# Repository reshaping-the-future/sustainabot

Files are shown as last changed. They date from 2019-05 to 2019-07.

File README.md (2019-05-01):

# Sustainabot
Sustainabot is a mini robot printer that uses everyday materials to create shapes and patterns.

The robot's body designs, circuit layouts, microcontroller code and accompanying Android app source code are all released under the Apache 2.0 license.

See the [toolkit website](http://digitalinclusiontoolkit.org/) and [research project website](http://www.reshapingthefuture.org/) for more details and related work.

## Building your own Sustainabot
Sustainabot is made up of several separate components, and each one is documented in more detail within the relevant source directory:

* [Device body](sustainabot-device/body)
* [Electronics and microcontroller code](sustainabot-device/controller)
* [Android controller app](sustainabot-android)

## License
Apache 2.0

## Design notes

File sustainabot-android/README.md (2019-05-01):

# Sustainabot controller app
Sustainabot's Android app allows you to configure the device's parameters and command it to draw images and diagrams.

The current version is configured to connect to a pre-set list of Sustainabot devices (by Bluetooth MAC address) for ease of use. Before running the application, set your own device IDs in [DeviceListActivity.java](app/src/main/java/app/akexorcist/bluetoothspp/library/DeviceListActivity.java). Alternatively, remove the MAC address checking in the `BroadcastReceiver` of the same file to display all available devices.

This app is intended to be used for local testing and material printing, rather than public release (e.g., on Google Play). If you would like to release the app publicly, you will need to change its package name. To do this, edit the `applicationId` field in the app module's [build.gradle](app/build.gradle).

## License
Apache 2.0

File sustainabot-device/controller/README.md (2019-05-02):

# Sustainabot controller
Sustainabot is controlled using a custom-made circuit board, which runs three micro planetary-drive geared motors and a Bluetooth module, provides magnetometer readings from its onboard sensor, and handles battery charging.

This repository provides [circuit diagrams](gerber), a [bill of materials](bill-of-materials.xlsx) and [parts coordinates list](parts-list-coordinates.xlsx), a [list of commands](command-list.txt), and [general hardware documentation](sustainabot-building.pdf).

You will also need the following (or similar), in addition to the circuit board:
* Three 700:1 micro planetary motors ([example](https://coolcomponents.co.uk/products/700-1-sub-micro-plastic-planetary-gearmotor))
* A Bluetooth HC-05 module
* A Lithium-polymer battery
* Optional: Two extra 100 kOhm resistors for the battery monitor feature

For simplicity, we have provided both the [source](sustainabot.bas) and [prebuilt](sustainabot.hex) embedded code. In order to deploy the prebuilt code, you will need a debugger (e.g., [PICkit 3](https://www.microchip.com/DevelopmentTools/ProductDetails/pg164130)) and the [MPLAB IDE](https://www.microchip.com/mplab/mplab-x-ide).

To deploy the prebuilt file using the MPLAB IDE:
1. File > New Project…
2. Select `Microchip Embedded` and `Prebuilt (Hex, Loadable Image) Project`, then press Next.
3. On the following page, configure the project:
    1. In the "Prebuilt Filename" box, select the `sustainabot.hex` file from this repository.
    2. For "Family", select `Advanced 8-bit MCUs (PIC18)`.
    3. For "Device", select `PIC18F26J53` (which you can copy and paste from here to ensure accuracy).
    4. In "Hardware Tool", select `PICkit3`, then press Next.
4. On the final page, select your chose of project location (or leave the default value), then press Finish
5. Once the project is loaded, edit its properties (i.e., via the right-click menu), and in "Conf: [default]" > "PICkit 3", select the "Power" item from the dropdown menu, selecting `Power target circuit from PICkit3` and setting the Voltage Level to `3.25`.
6. Plug in your assembled Sustainabot, ensuring that the central wire on the board's programmer port is routed to the indicator arrow on the PICkit 3)
7. Power on the Sustainabot, then connect the PICkit 3 to your computer
8. Click `Make and Program Device` in the MPLAB IDE

Once you have programmed your device, you can disconnect the programming cable and use the [android app](../../sustainabot-android) to control your Sustainabot.

## License
Apache 2.0

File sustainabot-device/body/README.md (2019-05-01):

# Sustainabot body
Sustainabot's body is made primarily from 3D-printed parts, with a laser-cut wheel adapter and a vinyl insert that helps material to flow smoothly.

The body is made up of the following components:
* The [main housing](body-main.stl), which holds all of the circuitry and electronics.
* A [chute cover](body-chute-cover.stl), which allows the chute motor to control material flow
* A [cable cover](body-cable-cover.stl), which tidies away all connecting wires.
* A [switch](body-switch-cover.stl), which enlarges the onboard on/off toggle to provide easier control.
* A [shelf](body-shelf.stl) and [cover](body-hopper-cover.stl), which keep all of the electonics enclosed, and make it easy to pour in printing material.
* A [wheel adapter](wheel-adapter.svg), which connects the LEGO wheels to the drive motors.
* A [vinyl insert](hopper-insert.svg), which makes a smooth internal surface to help with material flow.

In addition to the printed and laser-cut components listed above, and the [circuit board](../controller) (with its component parts, motors, battery and Bluetooth board), you will also need the following:
* A 6.35mm (1/4in) ceramic Si3N4 bearing ([example](https://www.amazon.co.uk/dp/B073XK257W))
* Two Ø15mm×6mm LEGO wheels (example [tyre](https://www.brickowl.com/catalog/lego-tire-15-x-6mm-with-offset-tread-band-around-center-of-tread-87414) and [rim](https://www.brickowl.com/catalog/lego-wheel-rim-8-x-6-4-without-side-notch-4624))
* Three small screws to secure the cable cover (though tape will also suffice)
* A metal stopper insert (to align the chute cover) – in our devices this was simply a small nail driven into its main body

## License
Apache 2.0

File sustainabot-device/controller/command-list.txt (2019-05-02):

Upon switch-on:
	Variables are initialised
	Wheel outputs to control H-bridges are set off/low 
	Duty cycle for the forward and backward motion PWMs are set to EEPROM stored values
	Magnetometer is initialised
	Green LED is switched on
	An array is filled with a trigonometric look-up table
	Listens for user-defined commands until “Go” command received
	Execute list of commands
	Check battery voltage (if 2-resistor battery mod fitted)
	Return to “Listens for user-defined commands”

Commands are sent from a phone or PC via Bluetooth/serial link as a series of 5 characters, each beginning with $, followed by the command character, and then 3 numerical digits i.e. $F030 

List of available commands (### values not used, xxx values are used):

Immediate commands (not added to the command list)
	J###		Display this list of commands
	L###		List commands currently stored in EEPROM
	C###		Clear all stored commands
	G###		Execute all stored commands
	0xxx (zero)	Perform a compass calibration for xxx turn units (calculate magnetometer offsets)
	Z###		Request current heading
	I###		Battery voltage request
	K###		Continuously seek random headings (until reed switch is triggered)
	t###		List wheel calibration and Drop/Stop values
	qxxx		Left wheel Forward set to xxx (duty cycle – 100 to 255)
	wxxx		Left wheel Backward set to xxx (duty cycle – 100 to 255)
	rxxx		Right wheel Forward set to xxx (duty cycle – 100 to 255)
	exxx		Right wheel Backward set to xxx (duty cycle – 100 to 255)
	Vxxx		Turning duration per unit (for Left/Right) to xxx
	uxxx		Turning duration per unit (for Heading) to xxx

Stored/sequence commands
	Fxxx		Forward by xxx units
	Bxxx		Backward by xxx units
	Oxxx		Left turn by xxx units
	Pxxx		Right turn by xxx units
	Hxxx		Turn to heading xxx degrees (0 – 255, not 0 – 359)
	axxx		Left wheel Forward set xxx (temporary; allow differential wheel speeds)
	sxxx		Left wheel Backward set xxx (temporary; allow differential wheel speeds) 
	dxxx		Right wheel Forward set xxx (temporary; allow differential wheel speeds)
	fxxx		Right wheel Backward set xxx (temporary; allow differential wheel speeds)
	gxxx		Reset forward/backward correction to stored values (make forward straight again) 
	D###		Start drop (uses chute open time defined by $Txxx)
	S###		Stop drop  (uses chute close time defined by $Sxxx)
	Txxx 		Chute open set to xxx (motor engaged for xxx time units)
	Uxxx 		Chute close set to xxx (motor engaged for xxx time units – likely longer than $Txxx) 
	Qxxx 		Perform Lane change (non-heading version) xxx = 1 for jitter 
	Rxxx 		Perform Lane change (Heading version) xxx = 1 for jitter
	4xxx 		Lane change var 1 set to xxx how much to initially move forward
	5xxx 		Lane change var 2 set to xxx how much to turn left
	6xxx 		Lane change var 3 set to xxx how much to move forward
	7xxx 		Lane change var 4 set to xxx how much to finally turn right

	@xxx 		Draw dots with xxx = number of dots to draw
	1xxx 		Draw dot var 1 set to xxx how much to initially move forward
	2xxx 		Draw dot var 2 set to xxx how much to move forward, chute open
	3xxx 		Draw dot var 3 set to xxx how much to initially move forward, chute closed
	8xxx 		Draw dot left/right correction (100+/-) after $9xxx dots, perform a left/right turn
	9xxx 		Draw dots, turn correction dot counter, before performing a turn correction 

	Ixxx 		Jitter strength set to xxx (How much the Sustainabot turns left/right when using Jitter)
	Exxx 		Jitter
	pxxx 		Pause (xxx * 50) milliseconds

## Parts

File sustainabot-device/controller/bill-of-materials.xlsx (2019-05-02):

Quantity | Designator | Description | Manufacturer | Manufacturer Part Number | Supplier 1 | Supplier Part Number 1 | Notes
2 | 16MHZ_X1, 16MHZ_X2 | 18 pF 25 V 0201 Capacitor | MuRata | GRM0335C1E180JA01D | Farnell | 1759056
2 | C_VCP, C_VCP1 | 10 nF 25 V 0201 X5R | MuRata | GRM033R61E103KA12D | Farnell | 2611885
1 | 5V_CAP_10N | 10 nF, 50 V, 0603 X7R | TDK | C1608X7R1H103K080AA | Mouser UK | 810-C1608X7R1H103K
3 | PIC_DECOUP, VUSB, ACC_DC2 | 100 nF, 10 V, 0201 X5R | MuRata | GRM033R61A104KE15D | Farnell | 2470450
1 | ACC_DC1 | 0.22 uF, 16 V, 0402 X5R | Multicomp | MC0402X224K160CT | Farnell | 1759389
3 | C_REGIN_3V3, C_VINT, C_VINT1 | 2.2 uF, 25 V, 1206 X7R | Multicomp | MC1206B225K250CT | Farnell | 2320884
1 | 5V_CAP_2.2 | Capacitor, 2.2 uF, 50 V, 1210 X7R | TDK | C3225X7R1H225K250AB | Mouser UK | 810-C3225X7R1H225K11
1 | ACC_DC4 | 4.7 uF, 6.3 V, 0603 X5R | Multicomp | MC0603X475K6R3CT | Farnell | 2320811
1 | ACC_DC3 | 10 uF, 4 V. 0402 X5R | MuRata | GRM155R60G106ME44D | Farnell | 2611904
2 | C_REGOUT_3V3, VDDCORE/VCAP | 10 uF, 10 V, 0805 X5R | Kemet | C0805C106K8PACTU | Farnell | 1463362
2 | C_VM, C_VM2 | 10 uF, 6.3 V, 0603 X5R | Samsung Electro-Mechanics | CL10A106MQ8NNNC | Digikey | 1276-1119-1-ND
1 | 5V_CAP_120 | 120 uF, 6.3 V, can 5 mm diam | United Chemi-Con | APXE6R3ARA121ME61G | Mouser UK | 661-APXE6R3A121ME61G
3 | RED_RES, GREEN_RES, YELLOW_RES | 68 ohm, 50 V, 0402 62.5 mW | Multicomp | MCWR04X68R0FTL | Farnell | 2447208
2 | SCL_PU, SDA_PU | 4.7 kohm, 25 V, 0201 50 mW | Multicomp | MCWR02X4701FAL | Farnell | 2447748
3 | RESET_PU, MCLR_PU, TS_PD1 | 10 kohm, 25 V, 0201 50 mW | Multicomp | MCRE000164 | Farnell | 1711641
2 | REED_PD, TS_PD2 | 51 kohm, 25 V, 0201 50 mW | Multicomp | MCRE000181 | Farnell | 1711661
1 | 3.3V_REG | LTC3531-3.3, TSOT23-6 | Linear Technology | LTC3531ES6-3.3#TRMPBF | Digikey | LTC3531ES6-3.3#TRMPBFCT-ND
1 | ACC_MAG | LSM303DLHC, LGA14 | STMicroelectronics | LSM303DLHCTR | Digikey | 497-11918-1-ND
1 | PIC_PROCESSOR | PIC18F26J53ML, QFN28 | Microchip technology | PIC18F26J53-I/ML | Digikey | PIC18F26J53-I/ML-ND
1 | MEMORY | 24AA1025, 8SOIC | Microchip technology | 24AA1025-I/SM | Digikey | 24AA1025-I/SM-ND
2 | DRIVE1, DRIVE2 | DRV8833, WQFN16 | Texas Instruments | DRV8833RTYR | Digikey | 296-29398-2-ND
1 | 16MHZ_XTAL | Xtal 2.5 x 2 mm | TXC | 8Z-16.000MAAJ-T | Farnell | 1842186
1 | GREEN_LED | LED Green | Kingbright | KINGBRIGHT KPT-2012SGC | Farnell | 2449883
1 | YELLOW_LED | LED Yellow | Kingbright | KINGBRIGHT KPT-2012SYCK | Farnell | 2099242
1 | RED_LED | LED Red | Kingbright | KINGBRIGHT KPT-2012SURCK | Farnell | 2099241
1 | INDUCTOR | Inductor, 10 uH, 0805 500 mA | TDK | MLZ2012N100LT000 | Digikey | 445-6762-1-ND
2 | BLUETOOTH, SERVO_CTRL | BLUETOOTH Bluetooth | Molex | 53047-0410 | Farnell | 9733060
1 | PGMR | PGMR Pgmr | Molex | 53047-0510 | Farnell | 9732861
1 | PUSH_BUTTON | BUTTON Push | Omron | B3U-1000P | Digikey | SW1020CT-ND
1 | REED_SWITCH | SWITCH Reed | Meder | MK24-A-3 | Mouser | 876-MK24-A-3
1 | SLIDER | SLIDER Slider | Copal | CUS-12B | Digikey | 563-1102-1-ND
1 | LIGHT_SENSE | APDS9007, Light sensor | Avago | APDS9007 | Digikey | 516-1719-1-ND | NO FIT
1 | REG_5V | LM22675, Buck, 5V | Texas Instruments | LM22675MR-5.0/NOPB | Digikey | LM22675MR-5.0/NOPB-ND
1 | INDUCTOR_5V | Inductor, 22 uH 2.5 A 75 mohm | Wurth Electronics | 744066220 | Mouser UK | 710-744066220
1 | DIODE | Schottky Rect, 60 V, 1 A DO-214AA 2 pin, 750 mV | TAIWAN SEMICONDUCTOR | SK16B | Farnell | 1299282

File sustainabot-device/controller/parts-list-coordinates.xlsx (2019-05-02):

Part | Value | Package | Position (mil) Orientation | Manufacturer | Manufacturer Part Number | Supplier 1 | Supplier Part Number 1
16MHZ_X1 | 18 pF 25 V 0201 Capacitor | 0201 | (-378.74016 -177.95276) R90 | MuRata | GRM0335C1E180JA01D | Farnell | 1759056
16MHZ_X2 | 18 pF 25 V 0201 Capacitor | 0201 | (-201.9685 -211.81102) R90 | MuRata | GRM0335C1E180JA01D | Farnell | 1759056
C_VCP | 10 nF 25 V 0201 X5R | 0201 | (-197.24409 -50.3937) MR270 | MuRata | GRM033R61E103KA12D | Farnell | 2611885
C_VCP1 | 10 nF 25 V 0201 X5R | 0201 | (-471.25984 -570.86614) MR90 | MuRata | GRM033R61E103KA12D | Farnell | 2611885
ACC_DC2 | 100 nF, 6.3 V, 0201 X5R | 0201 | (223.80155 -173.50554) R270 | AVX | 02016D104KAT2A | Farnell | 1657913
PIC_DECOUP | 100 nF, 6.3 V, 0201 X5R | 0201 | (123.34104 -144.23942) R270 | AVX | 02016D104KAT2A | Farnell | 1657913
VUSB | 100 nF, 6.3 V, 0201 X5R | 0201 | (-52.83711 -224.3157) R180 | AVX | 02016D104KAT2A | Farnell | 1657913
ACC_DC1 | 0.22 uF, 16 V, 0402 | 0402 | (301.98351 -155.75098) R180 | Multicomp | MC0402X224K160CT | Farnell | 1759389
USB_CHG_BAT1 | 1 uF, 10 V, 0402 X7S | 0402 | (-22 -561) MR0 | Murata | GCM155C71A105KE38D | Digikey | 490-13409-1-ND
C_VINT | 2.2 uF, 25 V, 1206 X7R | 1206 | (-86 -80) MR270 | Multicomp | MC1206B225K250CT | Farnell | 2320884
C_VINT1 | 2.2 uF, 25 V, 1206 X7R | 1206 | (-340.80623 -371.99126) MR0 | Multicomp | MC1206B225K250CT | Farnell | 2320884
C_REGIN_3V3 | 2.2 uF, 25 V, 1206 X7R | 1206 | (-459.63939 -714.86368) R90 | Multicomp | MC1206B225K250CT | Farnell | 2320884
ACC_DC4 | 4.7 uF, 6.3 V, 0603 Y5V | 0603 | (158.9487 -403.38349) R90 | Multicomp | MC0603F475Z6R3CT | Farnell | 2627457
USB_CHG_BAT | 4.7 uF, 4 V, 0402 X6S | 0402 | (250 -660) MR180 | TDK | C1005X6S0G475M050BC | Farnell | 2525033
USB_CHG_OUT | 4.7 uF, 4 V, 0402 X6S | 0402 | (228 -754) MR180 | TDK | C1005X6S0G475M050BC | Farnell | 2525033
ACC_DC3 | 10 uF, 4 V. 0402 X5R | 0402 | (137.94882 -207.18344) R0 | MuRata | GRM155R60G106ME44D | Farnell | 2611904
VDDCORE/VCAP | 10 uF, 10 V, 0805 Y5V | 0805 | (-429.44882 -184.71654) R90 | YAGEO | CC0805ZKY5V6BB106 | Farnell | 9402144
C_REGOUT_3V3 | 10 uF, 10 V, 0805 Y5V | 0805 | (-566.7142 -708.27571) R90 | YAGEO | CC0805ZKY5V6BB106 | Farnell | 9402144
C_VM | 10 uF, 6.3 V, 0603 X5R | 0603 | (-152.66929 -15) MR270 | YAGEO | CC0603MRX5R5BB106 | Farnell | 1458902
C_VM1 | 10 uF, 6.3 V, 0603 X5R | 0603 | (-517.71654 -519.29134) MR270 | YAGEO | CC0603MRX5R5BB106 | Farnell | 1458902
RED_RES | 68 ohm, 50 V, 0402 62.5 mW | 0402 | (278.05118 -98.91646) R180 | Multicomp | MCWR04X68R0FTL | Farnell | 2447208
YELLOW_RES | 68 ohm, 50 V, 0402 62.5 mW | 0402 | (30.34879 50.21641) MR180 | Multicomp | MCWR04X68R0FTL | Farnell | 2447208
GREEN_RES | 68 ohm, 50 V, 0402 62.5 mW | 0402 | (114.24877 -75.48339) MR90 | Multicomp | MCWR04X68R0FTL | Farnell | 2447208
PGOOD_LED_RES | 220 ohm, 50 V, 0402 62.5 mW | 0402 | (22 -596) R0 | Multicomp | MCWR04X2200FTL | Farnell | 2447136
CHG_LED_RES | 470 ohm, 50 V, 0402 62.5 mW | 0402 | (-54 -636) R270 | Multicomp | MCWR04X4700FTL | Farnell | 2447178
ISET_PD | 1.13 kohm, 50 V, 0402 62.5 mW | 0402 | (111 -535) MR0 | Multicomp | MCMR04X1131FTL | Farnell | 2072556
ILM_PD | 1.18 kohm, 50V, 0402 100 mW | 0402 | (-15 -606) MR0 | Panasonic | ERJ2RKF1181X | Farnell | 2302646
SCL_PU | 4.7 kohm, 25 V, 0201 50 mW | 0201 | (85.04897 -304.58354) R90 | Multicomp | MCWR02X4701FAL | Farnell | 2447748
SDA_PU | 4.7 kohm, 25 V, 0201 50 mW | 0201 | (167.48351 -123.95116) R0 | Multicomp | MCWR02X4701FAL | Farnell | 2447748
RESET_PU | 10 kohm, 25 V, 0201 50 mW | 0201 | (-573.24409 -628.6063) R90 | Multicomp | MCRE000164 | Farnell | 1711641
MCLR_PU | 10 kohm, 25 V, 0201 50 mW | 0201 | (-104.38472 73.88632) R180 | Multicomp | MCRE000164 | Farnell | 1711641
TS_PD | 10 kohm, 25 V, 0201 50 mW | 0201 | (190 -527) MR270 | Multicomp | MCRE000164 | Farnell | 1711641
TS_PD1 | 10 kohm, 25 V, 0201 50 mW | 0201 | (-238.74889 24.23782) R270 | Multicomp | MCRE000164 | Farnell | 1711641
REED_PD | 51 kohm, 25 V, 0201 50 mW | 0201 | (-57.18344 69.35113) R180 | Multicomp | MCRE000181 | Farnell | 1711661
TS_PD2 | 51 kohm, 25 V, 0201 50 mW | 0201 | (-245 -20) R90 | Multicomp | MCRE000181 | Farnell | 1711661
INDUCTOR | MLZ2012N100LT | 0805 | (-747.10236 -681.6378) R90 | TDK | MLZ2012N100LT | Digikey | 445-6762-1-ND
ACC_MAG | LSM303DLHC | LGA14 | (264.14875 -305.88349) R90 | STMicroelectronics | LSM303DLHCTR | Digikey | 497-11918-1-ND
CHARGED_BLUE_LED | 150060BS75000 | 1.6 x 0.7 mm | (101 -649) R90 | Wurth Elektronik | 150060BS75000 | Farnell | 2322069
CHARGING_ORANGE_LED | KP-2012SECK | 2 x 1.25 mm | (-3 -729) R180 | Kingbright | KP-2012SECK | Farnell | 2290332
GREEN_LED | KINGBRIGHT KPT-2012SGC | 2 x 1.25 mm | (160.14887 -9.88361) R180 | Kingbright | KINGBRIGHT KPT-2012SGC | Farnell | 2099239
RED_LED | KINGBRIGHT KPT-2012SURCK | 2 x 1.25 mm | (159.98339 -66.75111) R180 | Kingbright | KINGBRIGHT KPT-2012SURCK | Farnell | 2099241
YELLOW_LED | KINGBRIGHT KPT-2012SYCK | 2 x 1.25 mm | (159.92913 46.94488) R180 | Kingbright | KINGBRIGHT KPT-2012SYCK | Farnell | 2099242
DRIVE1 | DRV8833 | DRV8833 | (-320 -77) MR180 | Texas Instruments | DRV8833RTYR | Digikey | 296-29398-2-ND
DRIVE2 | DRV8833 | DRV8833 | (-352.3622 -546.85039) MR0 | Texas Instruments | DRV8833RTYR | Digikey | 296-29398-2-ND
3.3V_REG | LTC3531-3.3 | TSOT23-6 | (-656.22047 -686.6063) R0 | Linear Technology | LTC3531ES6-3.3#TRMPBF | Digikey | LTC3531ES6-3.3#TRMPBFCT-ND
MEMORY | 24AA1025 | 8SOIC | (-76.49988 -341.5) R270 | Microchip technology | 24AA1025-I/SM | Digikey | 24AA1025-I/SM-ND
PIC_PROCESSOR | PIC18F26J53ML | QFN28-ML_6X6MM | (-67.95116 -90.28334) R0 | Microchip technology | PIC18F26J53-I/ML | Digikey | PIC18F26J53-I/ML-ND
PUSH_BUTTON | B3U-1000P | B3U-1000P | (289.30709 13.50394) R90 | Omron | B3U-1000P | Digikey | SW1020CT-ND
REED_SWITCH | MK24-A-3 | MK24-A-3 | (4.65108 -185.91658) MR90 | Meder | MK24-A-3 | Mouser | 876-MK24-A-3
SLIDER | CUS-12B | CUS-12B | (-104.31238 -1032.12808) MR0 | Copal | CUS-12B | Digikey | 563-1102-1-ND
LIGHT_SENSE | APDS9007 | APDS-9007 | (-340.20472 -42.8189) R0 | Avago | APDS9007 | Digikey | 516-1719-1-ND
USB_CHRGR | BQ24074RGTR | BQ24074RGTR | (110 -649) MR0 | Texas Instruments | BQ24074RGTR | Digikey | 296-38873-1-ND
USB_SOCKET | ZX62RD-AB-5P8 | ZX62RD-AB-5P8 | (-550 -1031) MR0 | Hirose Connector | ZX62RD-AB-5P8 | Mouser UK | 798-ZX62RD-AB-5P830
16MHZ_XTAL | 16 MHz Xtal | 2.5 x 2 mm | (-301.30315 -218.28346) R270 | TXC | 8Z-16.000MAAJ-T | Farnell | 1842186
SERVO_CTRL | 53047-04 | 53047-04 | (198.77953 173) R180 | Molex | 53047-0410 | Farnell | 9733060
BLUETOOTH | 53047-04 | 53047-04 | (-640.13386 103.6063) R90 | Molex | 53047-0410 | Farnell | 9733060
PGMR | 53047-05 | 53047-05 | (-110 173) R180 | Molex | 53047-0510 | Farnell | 9732861
LIGHT_DIG | APDS9300 | APDS9300 | (223 -566) R0 | Avago | APDS-9300-020 | Digikey | 516-2134-1-ND

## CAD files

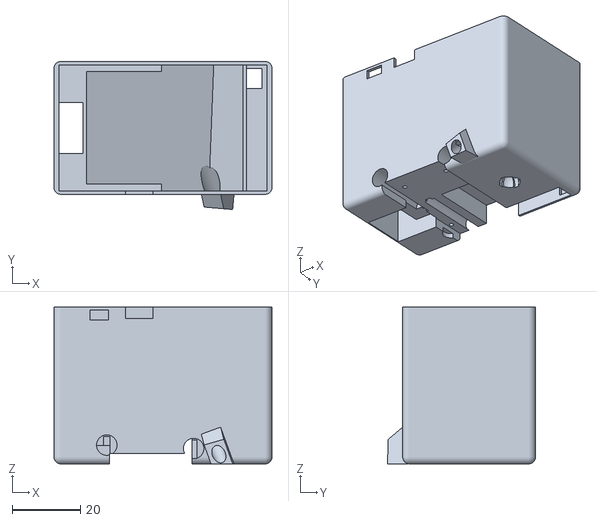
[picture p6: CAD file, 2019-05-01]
sustainabot-device/body/body-main.stl
64.0 x 43.5 x 46.0

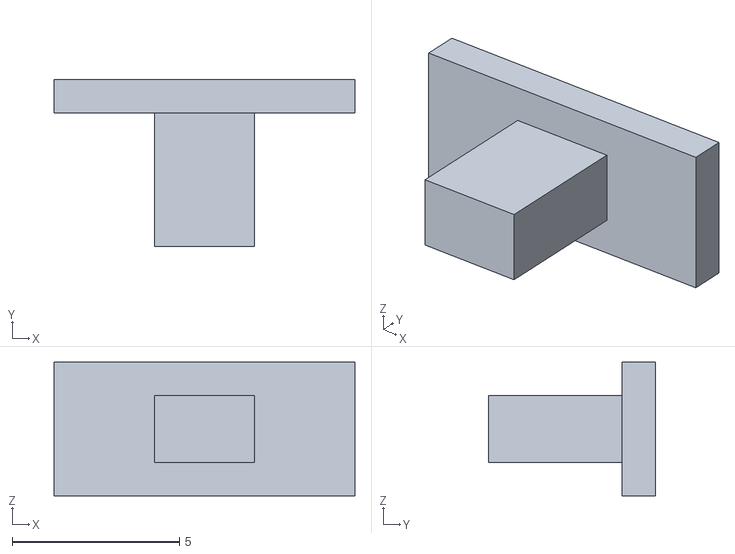
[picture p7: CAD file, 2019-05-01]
sustainabot-device/body/body-switch-cover.stl
9.00 x 5.00 x 4.00

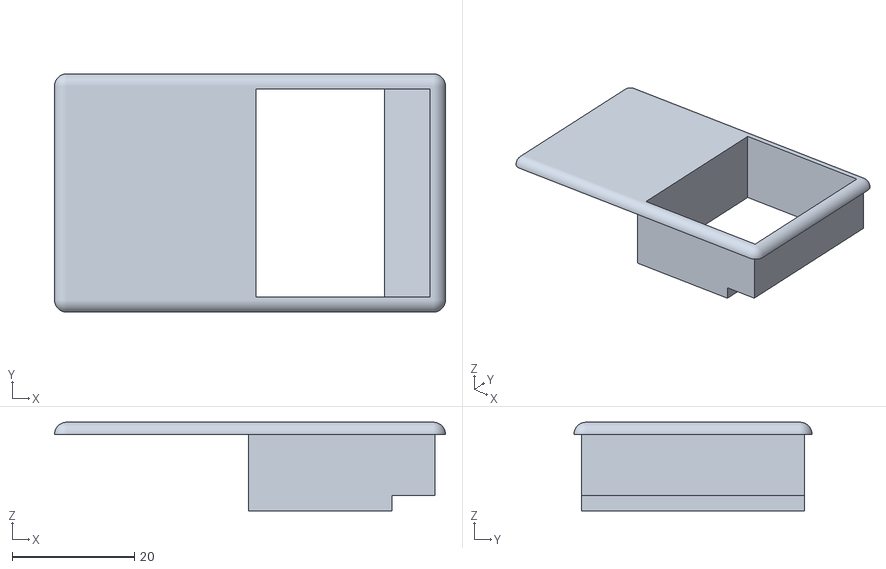
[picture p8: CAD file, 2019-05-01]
sustainabot-device/body/body-hopper-cover.stl
64.0 x 39.0 x 14.5

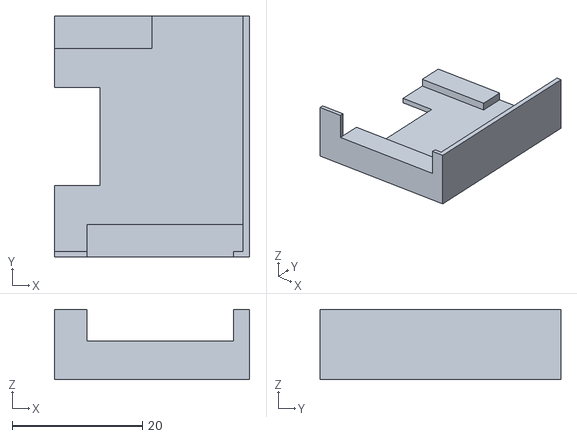
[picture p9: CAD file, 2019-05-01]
sustainabot-device/body/body-shelf.stl
30.0 x 37.0 x 10.8

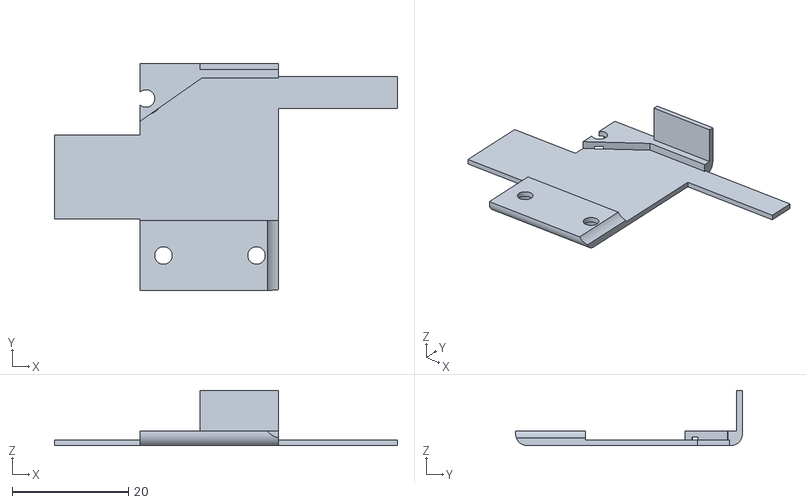
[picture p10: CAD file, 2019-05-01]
sustainabot-device/body/body-cable-cover.stl
59.0 x 39.0 x 9.50

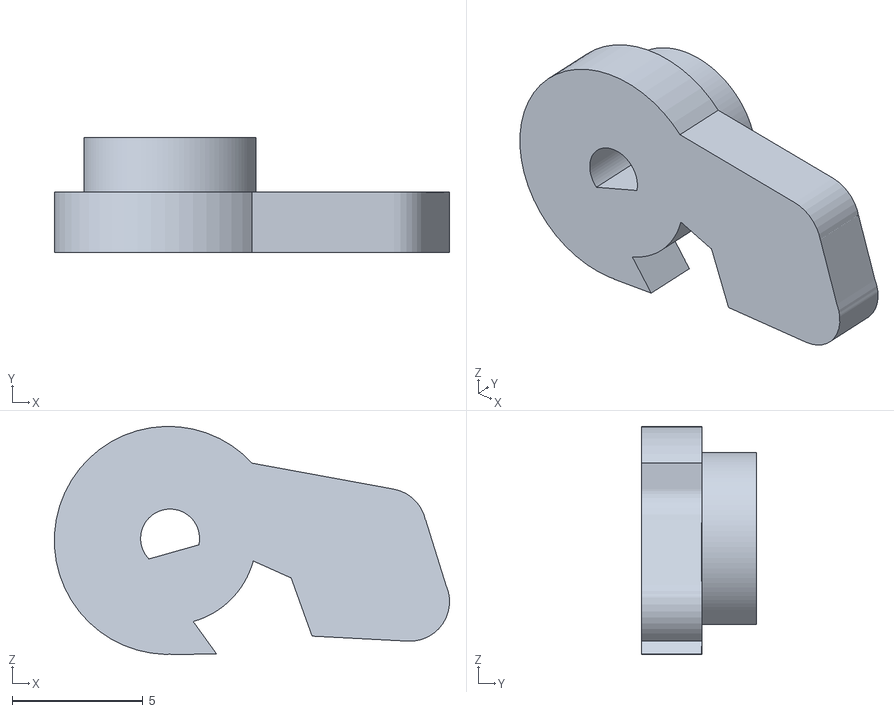
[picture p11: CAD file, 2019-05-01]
sustainabot-device/body/body-chute-cover.stl
15.1 x 4.41 x 8.74

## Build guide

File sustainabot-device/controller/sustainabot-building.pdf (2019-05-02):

### USB recharge socket (5V maximum)

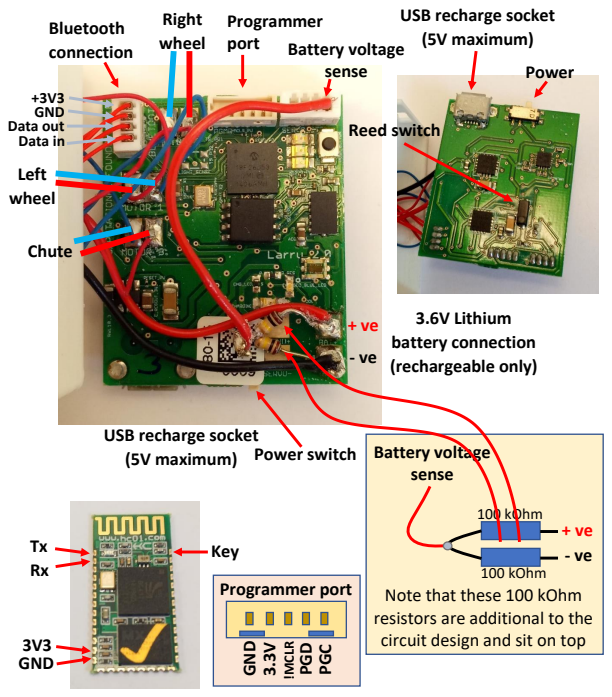
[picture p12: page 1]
Power; Bluetooth connection; +3V3 GND Data out Data in; Battery voltage sense; Right wheel; Left wheel; Chute; 3.6V Lithium battery connection (rechargeable only); 100 kOhm; Key Tx Rx; 3V3 GND; Programmer port; Reed switch

USB recharge socket
(5V maximum) Power switch

Programmer port GND 3.3V !MCLR PGD PG

Note that these 100 kOhm
resistors are additional to the
circuit design and sit on top

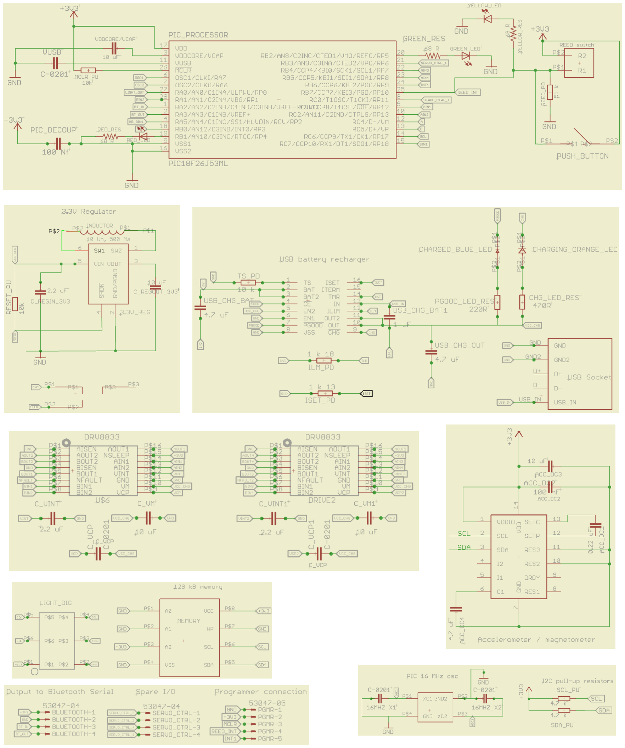
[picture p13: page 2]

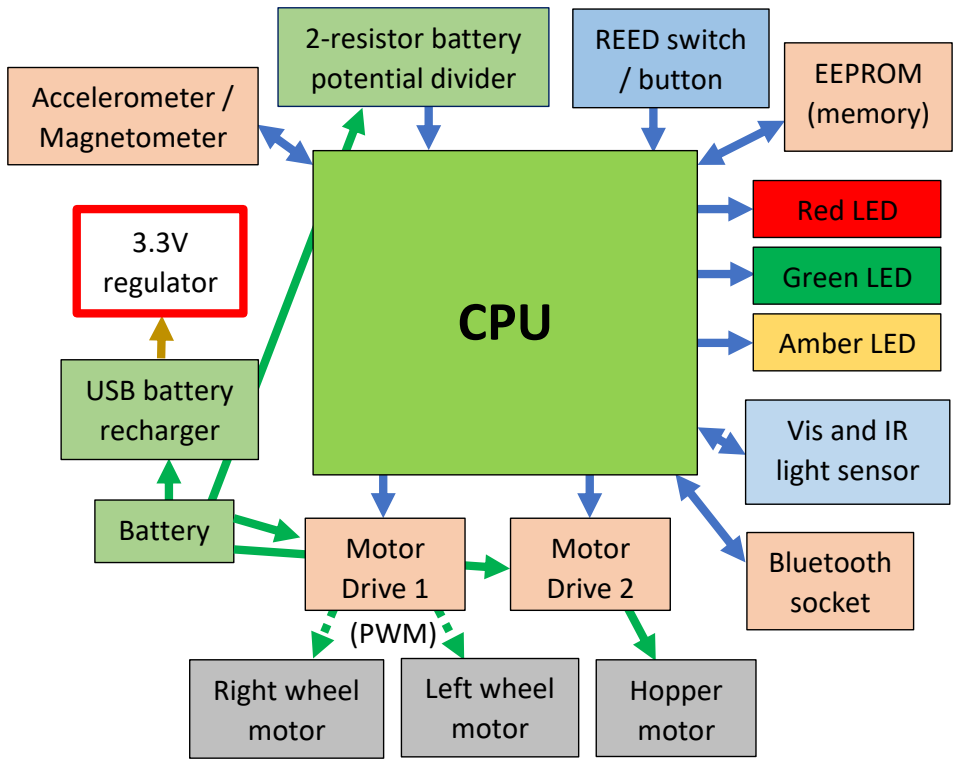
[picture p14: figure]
CPU; 3.3V regulator; USB battery recharger; REED switch / button; Red LED; Green LED; Amber LED; Bluetooth socket; 2-resistor battery potential divider; Vis and IR light sensor; EEPROM (memory) Accelerometer / Magnetometer; Battery; Motor; Drive 1; Motor Drive 2; Hopper motor; Left wheel motor; Right wheel motor; (PWM)
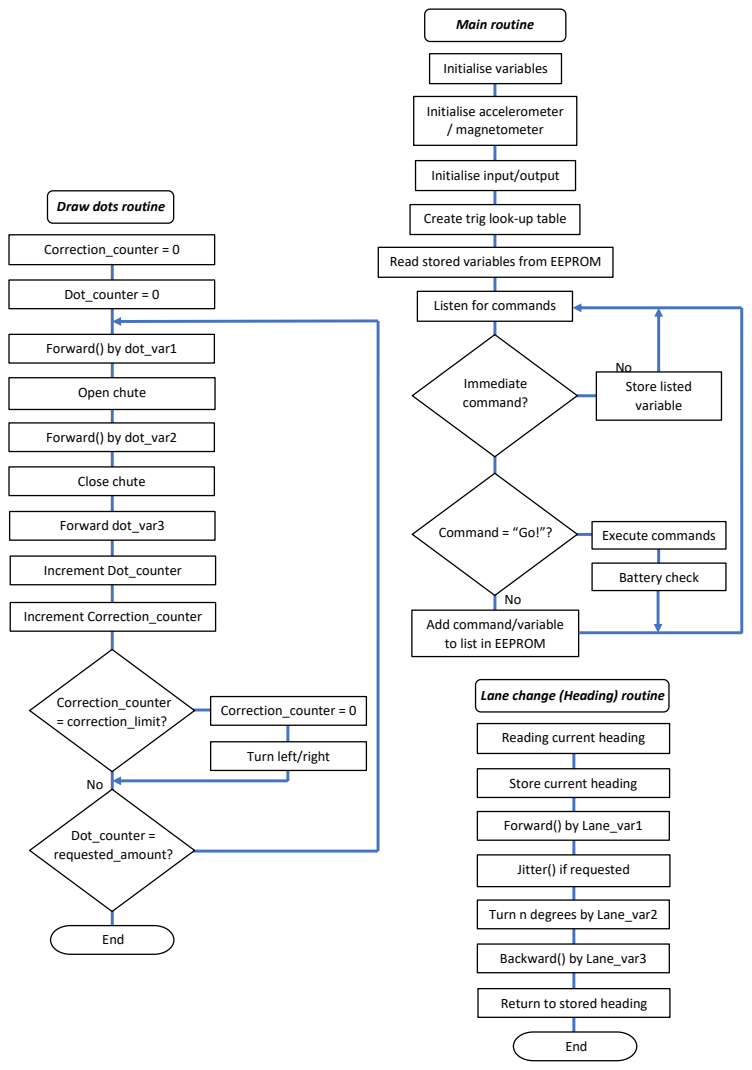
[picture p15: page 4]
Forward() by Lane_var1; End; Backward() by Lane_var3; Initialise variables; Initialise accelerometer / magnetometer; Store listed variable; Command = “Go!”?; Immediate command?; Execute commands; Battery check; Main routine; Correction_counter = 0; Dot_counter = 0; Forward() by dot_var1; Open chute; Forward() by dot_var2; Close chute; Forward dot_var3; Increment Dot_counter; Increment Correction_counter; Correction_counter; = correction_limit?; Dot_counter = requested_amount?

Initialise input/output

Draw dots routine

Create trig look-up table

Read stored variables from EEPROM

Listen for commands

Add command/variable
to list in EEPROM

Lane change (Heading) routine

Reading current heading

Turn left/right

Store current heading

Jitter() if requested

Turn n degrees by Lane_var2

Return to stored heading

Seek bearing routine

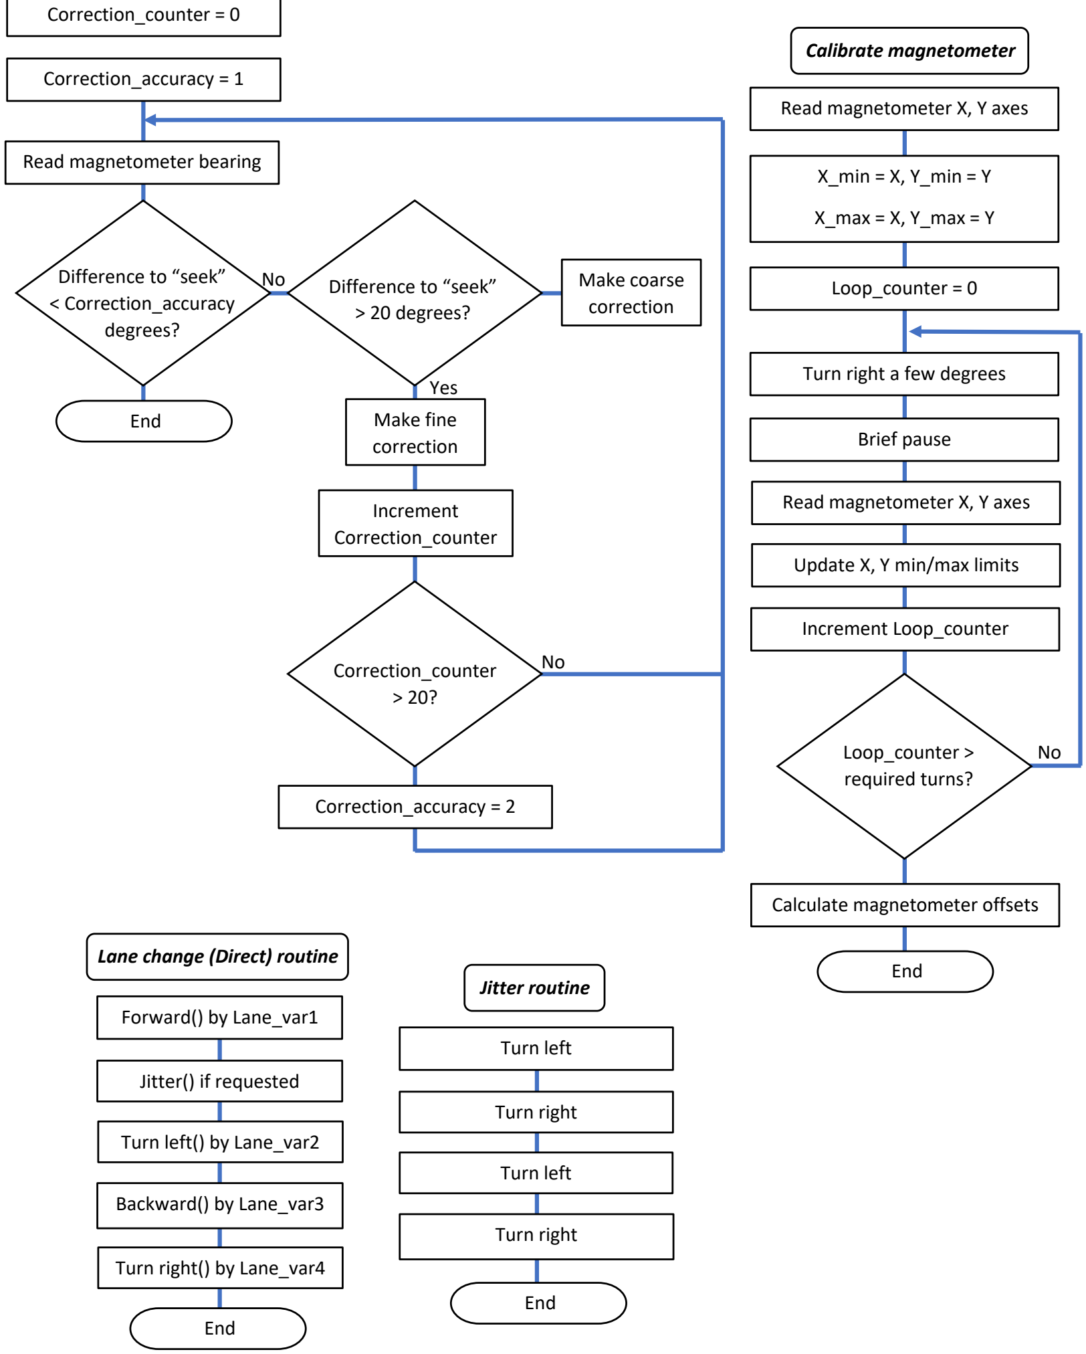
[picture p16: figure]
Lane change (Direct) routine; End; Forward() by Lane_var1; Jitter() if requested; Turn left() by Lane_var2; Backward() by Lane_var3; Turn right() by Lane_var4; Jitter routine; Turn left; Turn right; Read magnetometer bearing; Make coarse correction; Difference to “seek” < Correction_accuracy degrees?; Make fine correction; Increment Correction_counter; Correction_counter = 0; Correction_accuracy = 1; Yes; Correction_accuracy = 2; Difference to “seek” > 20 degrees?; Correction_counter > 20?; Calibrate magnetometer; Loop_counter = 0; Read magnetometer X, Y axes; X_min = X, Y_min = Y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

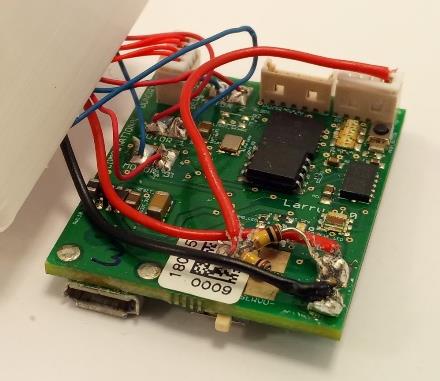
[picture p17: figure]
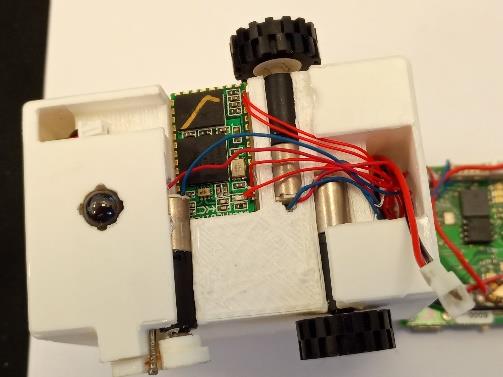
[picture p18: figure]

The Sustainabot circuit board, 29 x 36 x 10 mm, consists of two layers, with parts mounted on both top and bottom sides. These consist of a number of primary components, including a Microchip 8-bit microcontroller (PIC18F26J53) with multiple in-built timing modules, and highly flexible and programmable I/O ports. In addition to the CPU, there is an EEPROM (24AA1025 / 128kB) for storing command data,
MEMS accelerometer/magnetometer (LSM303DLHC) for determining compass heading, H-bridge DC motor drivers (DRV8833), digital visible light and infrared, dual light sensor (APDS9300), 3.3V/200 mA buck-boost regulator, and a lithium recharge controller chip (BQ24074RGTR). The CPU is clocked by an external 16 MHz crystal (PLL disabled), drives 3 coloured LEDs for status indication, transfers sensor data to/from MEMS sensors and EEPROM for storage via the I2C protocol, and enables various combinations of motor drive via the two dual-port H-bridge controllers (only 3 of the 4 ports connected in-circuit).

The battery monitor, while not necessary for the operation of the system, was added as an extra feature for the user. It simply consists of two 100 kOhm resistors, connected in-series across the battery terminals, with the centre tap feeding to one of the analogue input ports on the CPU. This is a simple potential divider (/2) enabling the overall battery potential to be measured with an ADC on the CPU, by utilising a reference of 3.3V from the board’s regulator. The firmware is configured to give the user a warning via the Bluetooth port when the voltage is at, or below, 3.3V, and that a recharge is required to maintain sufficient drive current to the wheel motors.

The Bluetooth module is an HC-05 board, used for transmission/reception of data. This was configured for serial communications at 38400 BAUD; any higher and the bit-error rate would have been too great due to mismatch from the CPU’s 16 MHz timing crystal. This board, or any similarly 3.3V powered Bluetooth serial communications board can be used in conjunction with the controller circuit.

Some of the CPU’s ports were reconfigured to make use of one of the internal timers, to output sub-microsecond-width pulses at frequencies of 100s of kHz. This, together with the ability to define different pulse-widths for different I/O ports that rapidly switch the H-bridge circuits on/off i.e. vary the ‘duty cycle’, enabled us to finely control the mean current delivered to each of the two motors, a technique commonly referred to as pulse width modulation (PWM). The H-bridge controllers in the circuit are configured to operate in two different modes. For the chute, this is in a full-on/off mode, while the drive wheels operate under PWM. The advantage of using PWM is that it also allows for compensation of different motor characteristics due to subtle size variations between the motors, in addition to independent drive at different speeds/directions for slow curved turning.

The drive motors we used on this device are 700:1 planetary-drive geared motors, lightweight, and with enough torque to manoeuvre a small robot around a flat surface.

The on-board magnetometer can be used to give the robot a sense of directionality, although, sensing magnetic fields can be prone to confusion due to ferrous material such as metal table legs, under-table support structures, all capable of causing a shift locally in the Earth’s magnetic field. This aside, the robot can be instructed to turn in a circle of more than 360 degrees, collecting magnetic data on the two axes parallel to the ground. From this, it is able to determine any hard- or soft-iron offsets and correct for them.

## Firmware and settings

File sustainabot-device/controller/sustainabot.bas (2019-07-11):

'***************************************************************************
'*  Name    : Sustainabot                                                *
'*  Author  : Mark Holton                                                  *
'*  Date    : 03 September 2018                                            *
'*  Version : 2.0                                                          *
'***************************************************************************

Include "modedefs.bas"
#CONFIG
    CONFIG XINST = OFF
    CONFIG CPUDIV = OSC1
	CONFIG WDTEN = ON
	CONFIG WDTPS = 512
    CONFIG ADCSEL = BIT12
	CONFIG RTCOSC = T1OSCREF
	CONFIG OSC = HS
	CONFIG CLKOEC = OFF
	CONFIG CFGPLLEN = OFF
	CONFIG CP0 = ON
	CONFIG IESO = ON
	CONFIG SOSCSEL = LOW
#ENDCONFIG
DEFINE      OSC 16
DEFINE      ADC_BITS 12
DEFINE      ADC_CLOCK 3
DEFINE      ADC_SAMPLEUS 200

trig_lu                         var byte[64]
command                         var byte[4]
command_store                   var byte[3072]

adval                           var word
pause_val                       var word
dot_counter                     var byte
dot_counter_point               var byte
cnt                             var word
batt_mon_av                     var long
batt_mon_av_read                var long
batt_test                       var byte
cnt2                            var word
cnt3                            var byte
magx                            VAR word
magy                            VAR word
magz                            VAR word
magx_accum                      VAR long
magy_accum                      VAR long
magz_accum                      VAR long
trig_lookup                     var word
mag_min_x                       var long
mag_min_y                       var long
mag_max_x                       var long
mag_max_y                       var long
tmp_mag                         var long
tmp_mag2                        var long
mag_magnitude                   var long
mag_magnitude_x                 var long
mag_magnitude_y                 var long
x_diff                          var long
rnd                             var word
y_diff                          var long
x_mag_off                       var long
y_mag_off                       var long
ratio                           var long
mag_sen_ctr                     var byte
mul_val                         var long
find_angctr                     var byte
lane_chg_jitter                 var byte
ang_val                         var byte
angle                           var byte
drop_fwd_cor                    var byte
right_fwd_width                 var word
left_fwd_width                  var word
right_bck_width                 var word
left_bck_width                  var word
heading_accuracy                var byte
ser_spd                         var byte
turn_timing_val                 var byte
turn_timing_heading_val         var byte
turn_timing_val_temp            var byte
turn_timing_val_store           var byte
calib_time                      var byte
scoop_amt                       var byte
scoop_amt2                      var byte
found_ang                       var byte
command_to_store                var byte
stored_heading                  var byte
jitter_time                     var byte
heading_search_cnt              VAR BYTE
chute_open                      var byte
draw_dot1                       var byte
draw_dot2                       var byte
draw_dot3                       var byte
lane_change1                    var byte
lane_change2                    var byte
lane_change3                    var byte
lane_change4                    var byte
lane_change_hdg_val             var byte
draw_dots_repeat                var byte
draw_dots_loop                  var byte
command_ptr                     var word
search_bearing                  var bit
command_value                   var byte
command_go                      var bit
cnt4                            var word
RW1                             var byte
RW2                             var byte
LW1                             var byte
LW2                             var byte
RWP1                            var latc.2
RWP2                            var latc.1
LWP1                            var latb.5
LWP2                            var latb.4

' set PWM duty cycle for each variable to 50% (left/right wheels, both forwards/backwards)
LW1         = 128
LW2         = 128  ' set PWM duty cycle variable to 50%
RW1         = 128  ' set PWM duty cycle variable to 50%
RW2         = 128  ' set PWM duty cycle variable to 50%

calib_time  = 150

i2c_add                         var     word
i2c_ctrl                        var     byte
i2c_ctrl_r                      var     byte

high portb.7

' enable / disable changes to output pin mapping in PIC
EECON2 = $55
EECON2 = $AA
PPSCON.0 = 0
RPOR13 = 14 ' remap PWM PXA to portc.2 (motor drive "AIN2")
EECON2 = $55
EECON2 = $AA
PPSCON.0 = 0

right_wheel1                    var CCPR1L
right_wheel2                    var CCPR8L
scoop2                          var lata.1
scoop1                          var latc.7
left_wheel1                     var CCPR5L
left_wheel2                     var CCPR4L

right_wheel1                    = 0  ' set PWM duty cycle to 0%
right_wheel2                    = 0  ' set PWM duty cycle to 0%
left_wheel1                     = 0  ' set PWM duty cycle to 0%
left_wheel2                     = 0  ' set PWM duty cycle to 0%

' PWM Mode selected for each of the 4 outputs (left/right wheels, both forwards/backwards)
CCP4CON                         = %00001100
CCP1CON                         = %00001100
CCP5CON                         = %00001100
CCP8CON                         = %00001100


T2CON                           = %00000000   ' Turn off timer2
INTCON.7                        = 0           ' Disable interrupts.
PR2                             = 255         ' PWM frequency.
T2CON                           = %00000100   ' Timer2 ON + 1:1 prescale

Serial_in                       var porta.2
green_led                       var portb.2
red_led                         var portb.1
yellow_led                      var portb.7
key_press                       var portb.7
i2cSDA                          VAR PORTB.0
i2cSCL                          VAR PORTC.6
Serial_out                      var porta.3

ancon0                          = %11111111 ' bit 3 is VREF+ analogue here but is set to digital ('1') if GPS is in use for GPS to DD comm's
ancon1                          = %00011111 ' ignore this bit -> set bit 3 as 0 for analogue input on portc.2 (ch11) or 1 for digital (GPS to DD comm's)
ADCON0                          = %00101111
adcon1.7                        = 1
adcon0.7                        = 0
adcon0.6                        = 0

porta.2                         = 0

jitter_time                     = 20
turn_timing_heading_val         = 8
dot_counter_point               = 5
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

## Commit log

2019-05-01 Initial import
    [body-cable-cover.stl, body-chute-cover.stl, body-hopper-cover.stl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]
2019-05-02 Added missing hardware files; updated documentation
    [bill-of-materials.xlsx, parts-list-coordinates.xlsx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]
2019-07-11 Fixed a minor bug in microcontroller source (already fixed in .hex) Added more detailed explanation of robot commands
    [sustainabot.bas]
